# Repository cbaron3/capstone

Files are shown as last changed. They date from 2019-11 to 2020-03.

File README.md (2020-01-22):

# Capstone
Source code for Mechatronic Systems Engineering Capstone project

# Requirements

## Teensyduino

Firmware is written for a Teensy 3.2 and makes use of Teensy features such as PWMServo and elapsedMicros. 

[Teensyduino](https://www.pjrc.com/teensy/teensyduino.html)

## Barometer

Library to interact with the on-board MPL3115A2. 

[MPL3115A2](https://github.com/sparkfun/MPL3115A2_Breakout/tree/master/Libraries/Arduino)

## GPS

Libraries to interact with the on-board Adafruit GPS module. Two were selected: one interrupt-based and one polling-based. The interrupt-based library is what we use.

[Adafruit_GPS - Interrupt based](https://github.com/adafruit/Adafruit_GPS)

[TinyGPS - Polling based](https://github.com/mikalhart/TinyGPS)

## IMU

Library to interact with the on-board MPU9250.

[MPU9250](https://github.com/bolderflight/MPU9250)

## AHRS 

Library to filter our raw IMU data to produce accurate roll/pitch/yaw.

[uNavAHR](https://github.com/bolderflight/uNavAHRS)

[Eigen - Library Dependency](https://github.com/bolderflight/Eigen)

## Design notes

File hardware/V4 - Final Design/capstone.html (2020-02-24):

Partlist exported from C:/Users/cbaro/OneDrive/Documents/Development/aero/capstone/hardware/V4 - Final Design/capstone.sch at 2020-02-19 5:00 PM

Qty | Value | Device | Package | Parts | Description | CREATED_BY | DESCRIPTION | DIGI-KEY_PART_NUMBER | DIGI-KEY_PURCHASE_URL | DIGIKEY_PART_NUMBER | DIGI_KEY_PART_NUMBER | MANUFACTURER | MF | MP | MPN | OC_FARNELL | OC_NEWARK | PACKAGE | POPULARITY | SPICEPREFIX | TP_SIGNAL_NAME
1 | | ANTENNA | PAD-01 | ANT1 | Antenna | | | | | | | | | | | | | | 11
1 | | GPS_FGPMMOPA6H | FGPMMOPA6H | U4 | GPS Module - MTK MT3339 Chipset, -165dBm sensitivity, 22 channels, 10Hz, auto-select external antenna options
1 | | W237-102 | W237-102 | X1 | WAGO SCREW CLAMP | | | | | | | | | | 237-102 | unknown | 70K9898 | | 32
1 | 0.1u | C-USC0603 | C0603 | C3 | CAPACITOR, American symbol
1 | 10 nF | C-USC0603 | C0603 | C9 | CAPACITOR, American symbol
2 | 10 u | C-USC0603 | C0603 | C1, C4 | CAPACITOR, American symbol
1 | 100 n | C-USC0603 | C0603 | C2 | CAPACITOR, American symbol
2 | 100 nF | C-USC0603 | C0603 | C7, C8 | CAPACITOR, American symbol
2 | 100n | C-USC0603 | C0603 | C5, C6 | CAPACITOR, American symbol | | | | | | | | | | | | | | 37 | C
2 | 4.7k | R-US_R0603 | R0603 | R3, R4 | RESISTOR, American symbol
1 | 470 | R-US_R0603 | R0603 | R10 | RESISTOR, American symbol
3 | 61300311121 | 61300311121 | 61300311121 | J1, J2, J3 | CONN HEADER VERT 3POS 2.54MM | PCBLayout.com | | | | | 732-5316-ND | Wurth Electronics Inc. | | | 61300311121
4 | 82 Ohm | R-US_R0603 | R0603 | R1, R2, R11, R12 | RESISTOR, American symbol
1 | BMP388 | BMP388 | PQFN50P200X200X80-10N | U1 | P-Sensor SPI I2C 1, 25 Bar SMD | | P-Sensor SPI I2C 1, 25 Bar SMD | 828-1079-1-ND | https://www.digikey.ca/product-detail/en/bosch-sensortec/BMP388/828-1079-1-ND/8322640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 | | | | Bosch Sensortec | BMP388 | | | | WFLGA-10 Bosch Tools
1 | CH291-1220LF | CH291-1220LF | CH291-1220LF | G1 | Battery Holder, SMT, 12mm | | | | | | | | | | | | | | 1
5 | HSMH-C190 | HSMH-C190 | LED-0603 | LED1, LED2, LED3, LED4, LED5 | LED RED DIFFUSED CHIP SMD | PCBLayout.com | | | | 516-1420-1-ND | | Broadcom Limited | | | HSMH-C190 | | | 0603
1 | LSM9DS1TR | LSM9DS1TR | PQFN43P300X350X102-24N | U2 | The LSM9DS1 is a system-in-package featuring a | | LSM9DS1 Series ±2/±4/±8/±16 g 3D Digital Linear Acceleration Sensor - LGA-24 | 497-14946-1-ND | https://www.digikey.ca/product-detail/en/stmicroelectronics/LSM9DS1TR/497-14946-1-ND/4988079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 | | | | STMicroelectronics | LSM9DS1TR | | | | TFLGA-24 STMicroelectronics
4 | MOUNT-HOLE2.8 | MOUNT-HOLE2.8 | 2,8 | H1, H2, H3, H4 | MOUNTING HOLE with drill center marker
18 | PTR1B1,27 | PTR1B1,27 | B1,27 | TP1, TP2, TP3, TP4, TP5, TP6, TP7, TP8, TP9, TP10, TP11, TP12, TP13, TP14, TP15, TP16, TP17, TP18 | TEST PIN
1 | RFM95W-915S2 | RFM95W-915S2 | XCVR_RFM95W-915S2 | U3 | RFM95(W) - Low Power Long Range Transceiver Module V1.0 | | RFM95W LoRA Transceiver Module 915MHz | RFM95W-915S2-ND | https://www.digikey.ca/product-detail/en/rf-solutions/RFM95W-915S2/RFM95W-915S2-ND/6564923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 | | | | RF Solutions | RFM95W-915S2 | | | | SMD-16 RF Solutions
1 | TEENSY_3.1-3.2_OUTER_ROW | TEENSY_3.1-3.2_OUTER_ROW | TEENSY_3.0-3.2&LC_OUTER_ROW | U$1 | Footprint for Teensy 3.1 or 3.2 board using all pin connections on the outer perimeter

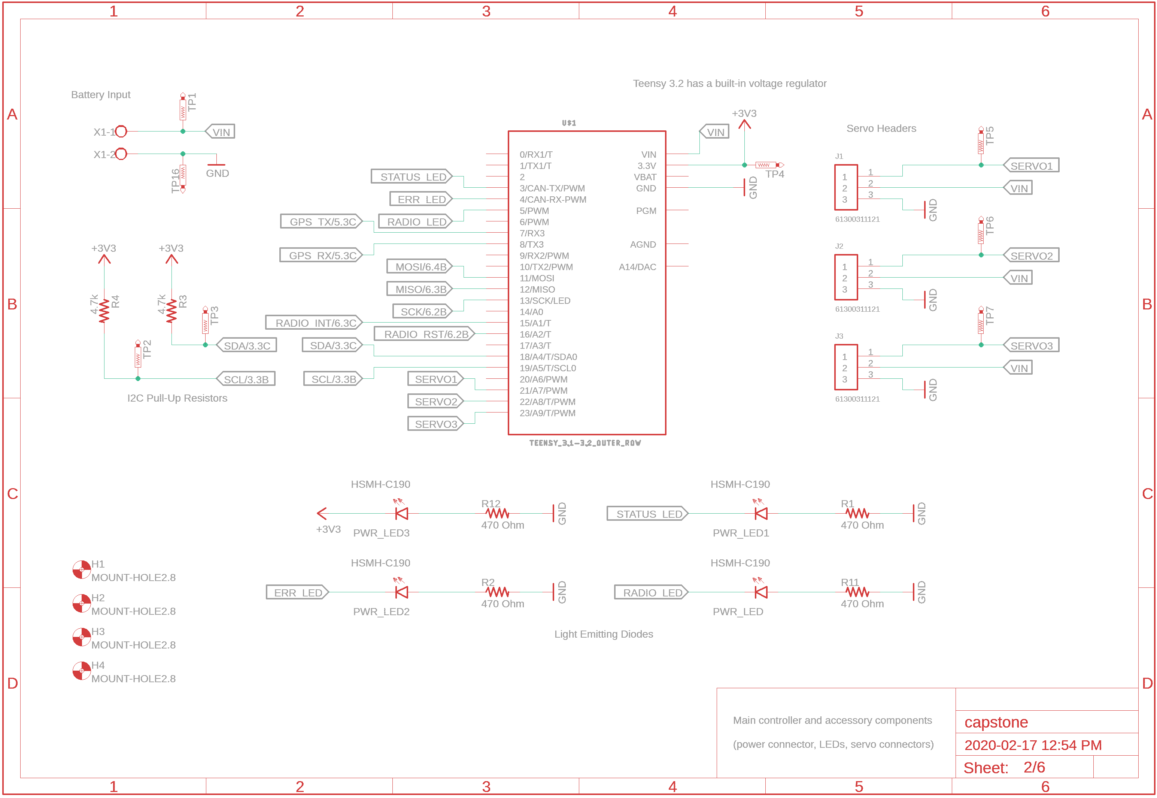
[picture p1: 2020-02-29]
hardware/V4 - Final Design/pics/teensy.png

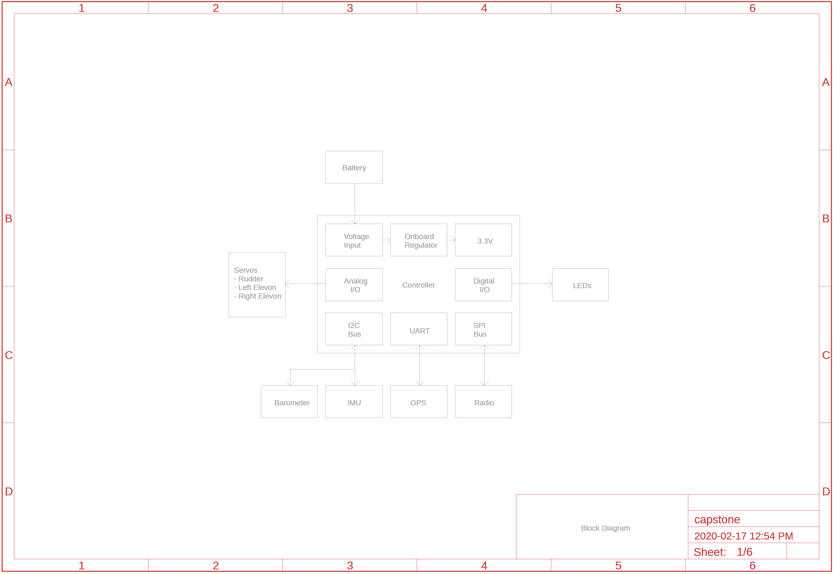
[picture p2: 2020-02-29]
hardware/V4 - Final Design/pics/block-diagram.png

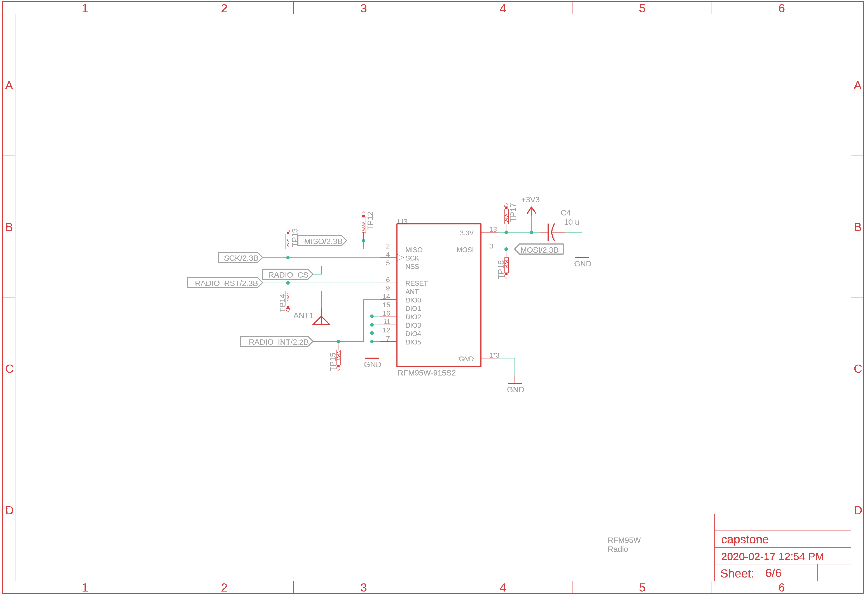
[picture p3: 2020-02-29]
hardware/V4 - Final Design/pics/radio.png

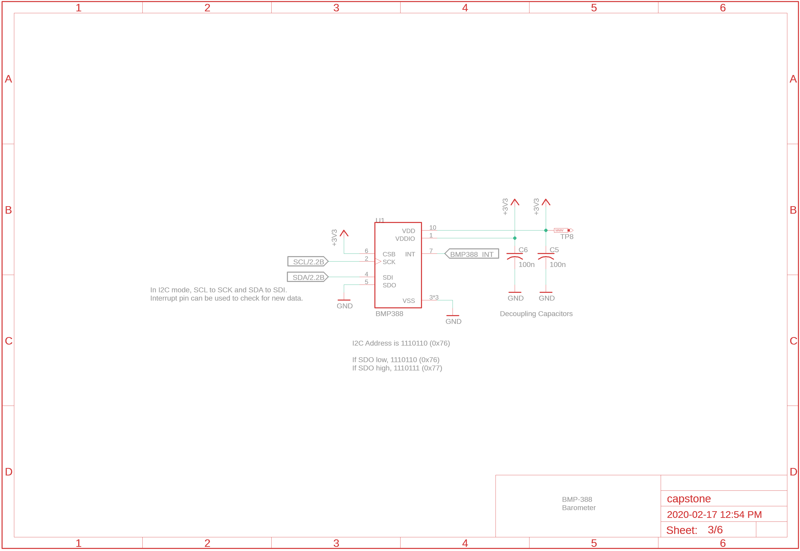
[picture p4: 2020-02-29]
hardware/V4 - Final Design/pics/bmp-388.png

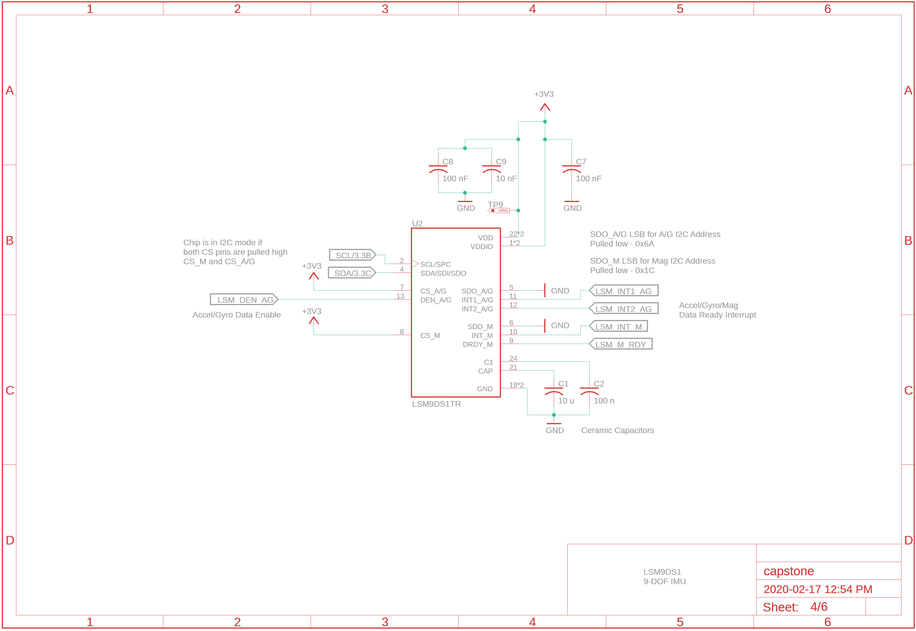
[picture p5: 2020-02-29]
hardware/V4 - Final Design/pics/imu.png

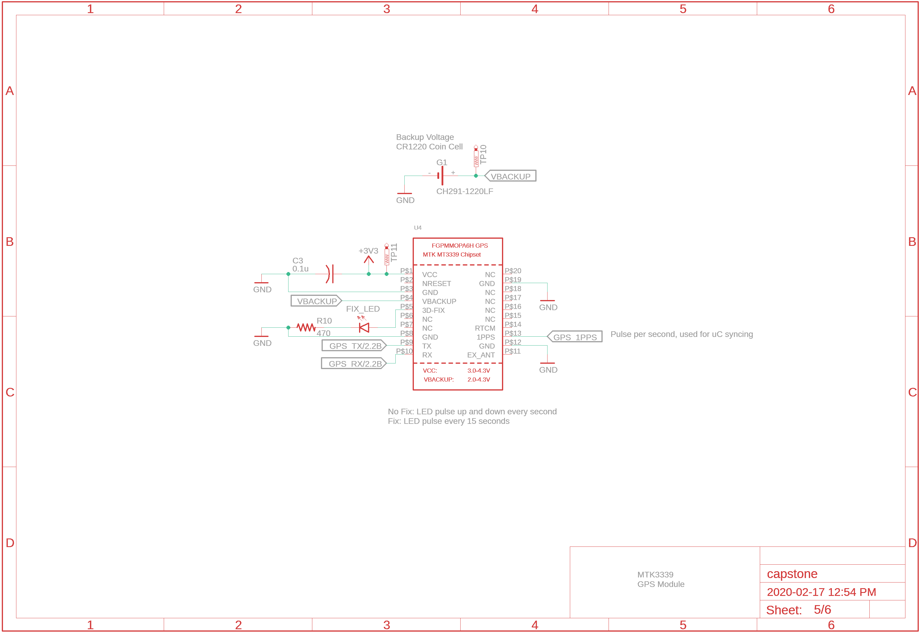
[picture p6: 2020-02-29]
hardware/V4 - Final Design/pics/gps.png

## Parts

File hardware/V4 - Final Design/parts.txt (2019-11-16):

IMU - (LSM9DS1TR) https://www.digikey.ca/product-detail/en/stmicroelectronics/LSM9DS1TR/497-14946-1-ND/4988079
Radio - (RFM95W) https://www.digikey.ca/product-detail/en/rf-solutions/RFM95W-915S2/RFM95W-915S2-ND/6564923
Baro - (BMP388) https://www.digikey.ca/product-detail/en/bosch-sensortec/BMP388/828-1079-1-ND/8322640
GPS - (Adafruit Ultimate GPS) https://www.adafruit.com/product/790
uC - Teensy 3.2

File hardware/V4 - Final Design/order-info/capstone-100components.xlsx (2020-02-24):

Index | Quantity | Part Number | Manufacturer Part Number | Description | Customer Reference | Available | Backorder | Unit Price | Extended Price CAD
1 | 100 | 732-10955-ND | 691137710002 | TERM BLK 2POS SIDE ENTRY 5MM PCB |  | 100 | 0 | 0.3861 | 38.61
2 | 300 | 399-8990-1-ND | C0603C103M4RACTU | CAP CER 10000PF 16V X7R 0603 |  | 300 | 0 | 0.0496 | 14.88
3 | 600 | 399-1098-1-ND | C0603C104Z4VACTU | CAP CER 0.1UF 16V Y5V 0603 |  | 600 | 0 | 0.019 | 11.40
4 | 100 | P470GCT-ND | ERJ-3GEYJ471V | RES SMD 470 OHM 5% 1/10W 0603 |  | 100 | 0 | 0.0292 | 2.92
5 | 200 | P4.70KHCT-ND | ERJ-3EKF4701V | RES SMD 4.7K OHM 1% 1/10W 0603 |  | 200 | 0 | 0.0356 | 7.12
6 | 400 | P82GCT-ND | ERJ-3GEYJ820V | RES SMD 82 OHM 5% 1/10W 0603 |  | 400 | 0 | 0.0238 | 9.52
7 | 500 | 732-4978-1-ND | 150060RS75000 | LED RED CLEAR 0603 SMD |  | 500 | 0 | 0.14156 | 70.78
8 | 100 | BK-885-ND | BK-885 | BATTERY RETAINER COIN 12MM SMD |  | 100 | 0 | 0.419 | 41.90
9 | 100 | 1568-1231-ND | DEV-13736 | TEENSY 3.2 K20 EVAL BRD |  | 100 | 0 | 32.17 | 3217.00
10 | 100 | RFM95W-868S2-ND | RFM95W-868S2 | RF TXRX MODULE ISM<1GHZ |  | 100 | 0 | 22.2 | 2220.00
11 | 100 | 497-14946-1-ND | LSM9DS1TR | IMU ACCEL/GYRO/MAG I2C/SPI 24LGA |  | 100 | 0 | 7.6955 | 769.55
12 | 100 | 828-1079-1-ND | BMP388 | SENSOR PRESSURE ABS |  | 100 | 0 | 3.1608 | 316.08
13 | 300 | 1849-1003-ND | PR20203VBNN | CONN HEADER VERT 3POS 2.54MM |  | 300 | 0 | 0.0473 | 14.19
 |  |  |  |  |  |  |  |  | 6733.95

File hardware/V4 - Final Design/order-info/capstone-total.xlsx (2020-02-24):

Quantity | Board Cost | Component Cost | Total Cost | Cost Per Board
10 | $61.11 | $1112 | $1173.11 | $117.31
25 | $89.23 | $2736.03 | $2825.26 | $113.01
50 | $121.62 | $5428.87 | $5550.49 | $111.01
100 | $182.82 | $10699.95 | $10882.77 | $108.83
500 | $629.33 | $52600.69 | $53230.02 | $106.46

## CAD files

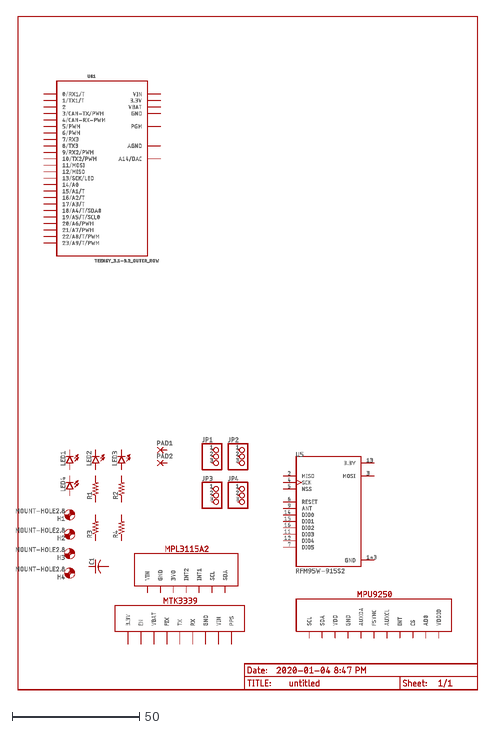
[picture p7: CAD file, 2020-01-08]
hardware/V5 - Prototype Design/untitled.dxf
181.2 x 264.5

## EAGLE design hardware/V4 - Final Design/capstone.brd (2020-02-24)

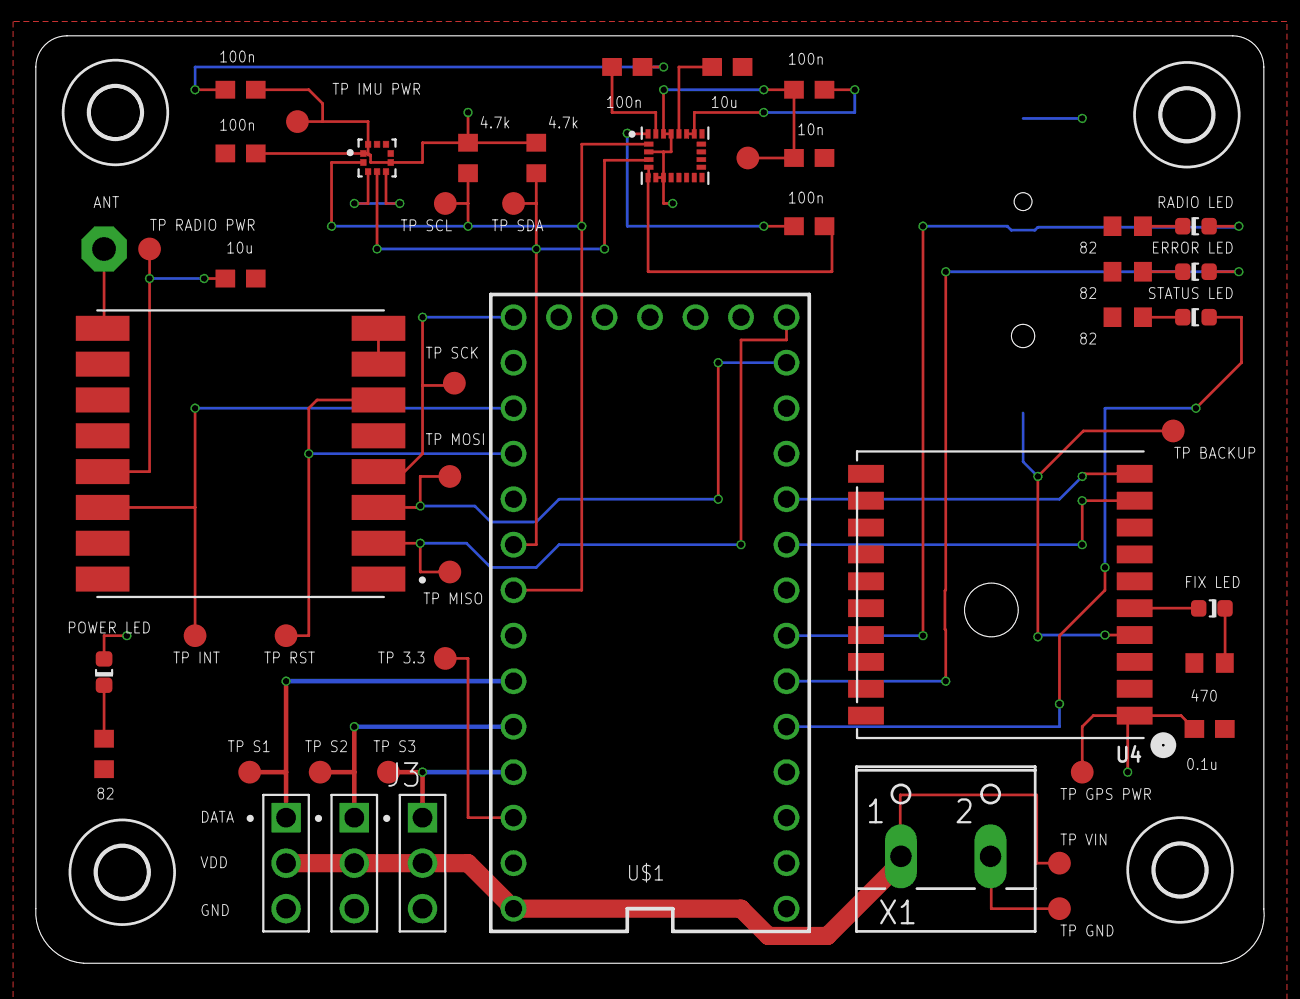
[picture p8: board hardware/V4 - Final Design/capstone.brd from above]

Board: 2 copper layers, 68.6 x 51.8 mm, 54 parts (1 on the bottom side), 28 nets.

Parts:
ANT1: PAD-01
C1, C4: 10 u; C0603
C2: 100 n; C0603
C3: 0.1u; C0603
C5, C6: 100n; C0603
C7, C8: 100 nF; C0603
C9: 10 nF; C0603
G1: CH291-1220LF
H1, H2, H3, H4: MOUNT-HOLE2.8; 2,8
J1, J2, J3: 61300311121
LED1, LED2, LED3, LED4, LED5: HSMH-C190; LED-0603
R1, R2, R11, R12: 82 Ohm; R0603
R3, R4: 4.7k; R0603
R10: 470; R0603
TP1, TP2, TP3, TP4, TP5, TP6, TP7, TP8, TP9, TP10, TP11, TP12, TP13, TP14, TP15, TP16, TP17, TP18: PTR1B1,27; B1,27
U1: BMP388; PQFN50P200X200X80-10N
U2: LSM9DS1TR; PQFN43P300X350X102-24N
U3: RFM95W-915S2; XCVR_RFM95W-915S2
U4: FGPMMOPA6H
U$1: TEENSY_3.1-3.2_OUTER_ROW; TEENSY_3.0-3.2&LC_OUTER_ROW
X1: W237-102

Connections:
+3V3: C3.1, C4.1, C5.1, C6.1, C7.1, C8.1, C9.1, LED1.A, R3.1, R4.1, TP4.TP, TP8.TP, TP9.TP, TP11.TP, TP17.TP, U1.1, U1.6, U1.10, U2.1, U2.3, U2.7, U2.8, U2.22, U2.23, U3.13, U4.P$1, U$1.3.3V, U$1.3.3V1
ERR_LED: LED2.A, U$1.4
GND: C1.2, C2.2, C3.2, C4.2, C5.2, C6.2, C7.2, C8.2, C9.2, G1.-, J1.3, J2.3, J3.3, R1.2, R2.2, R10.1, R11.2, R12.2, TP16.TP, U1.3, U1.5, U1.8, U1.9, U2.5, U2.6, U2.19, U2.20, U3.1, U3.7, U3.8, U3.10, U3.11, U3.12, U3.15, U3.16, U4.P$3, U4.P$8, U4.P$12, U4.P$19, U$1.GND, U$1.GND1, X1.2
GPS_RX: U4.P$10, U$1.8
GPS_TX: U4.P$9, U$1.7
MISO: TP12.TP, U3.2, U$1.12
MOSI: TP18.TP, U3.3, U$1.11
unnamed: C1.1, U2.21
unnamed: C2.1, U2.24
unnamed: LED5.C, R10.2
unnamed: LED5.A, U4.P$5
unnamed: ANT1.1, U3.9
unnamed: LED1.C, R12.1
unnamed: LED2.C, R2.1
unnamed: LED4.C, R11.1
unnamed: LED3.C, R1.1
RADIO_INT: TP15.TP, U3.14, U$1.15/A1
RADIO_LED: LED4.A, U$1.5
RADIO_RST: TP14.TP, U3.6, U$1.16/A2
SCK: TP13.TP, U3.4, U$1.13
SCL: R4.2, TP2.TP, U1.2, U2.2, U$1.19/A5
SDA: R3.2, TP3.TP, U1.4, U2.4, U$1.18/A4
SERVO1: J1.1, TP5.TP, U$1.21/A7
SERVO2: J2.1, TP6.TP, U$1.22/A8
SERVO3: J3.1, TP7.TP, U$1.23/A9
STATUS_LED: LED3.A, U$1.3
VBACKUP: G1.+, TP10.TP, U4.P$4
VIN: J1.2, J2.2, J3.2, TP1.TP, U$1.VIN, X1.1

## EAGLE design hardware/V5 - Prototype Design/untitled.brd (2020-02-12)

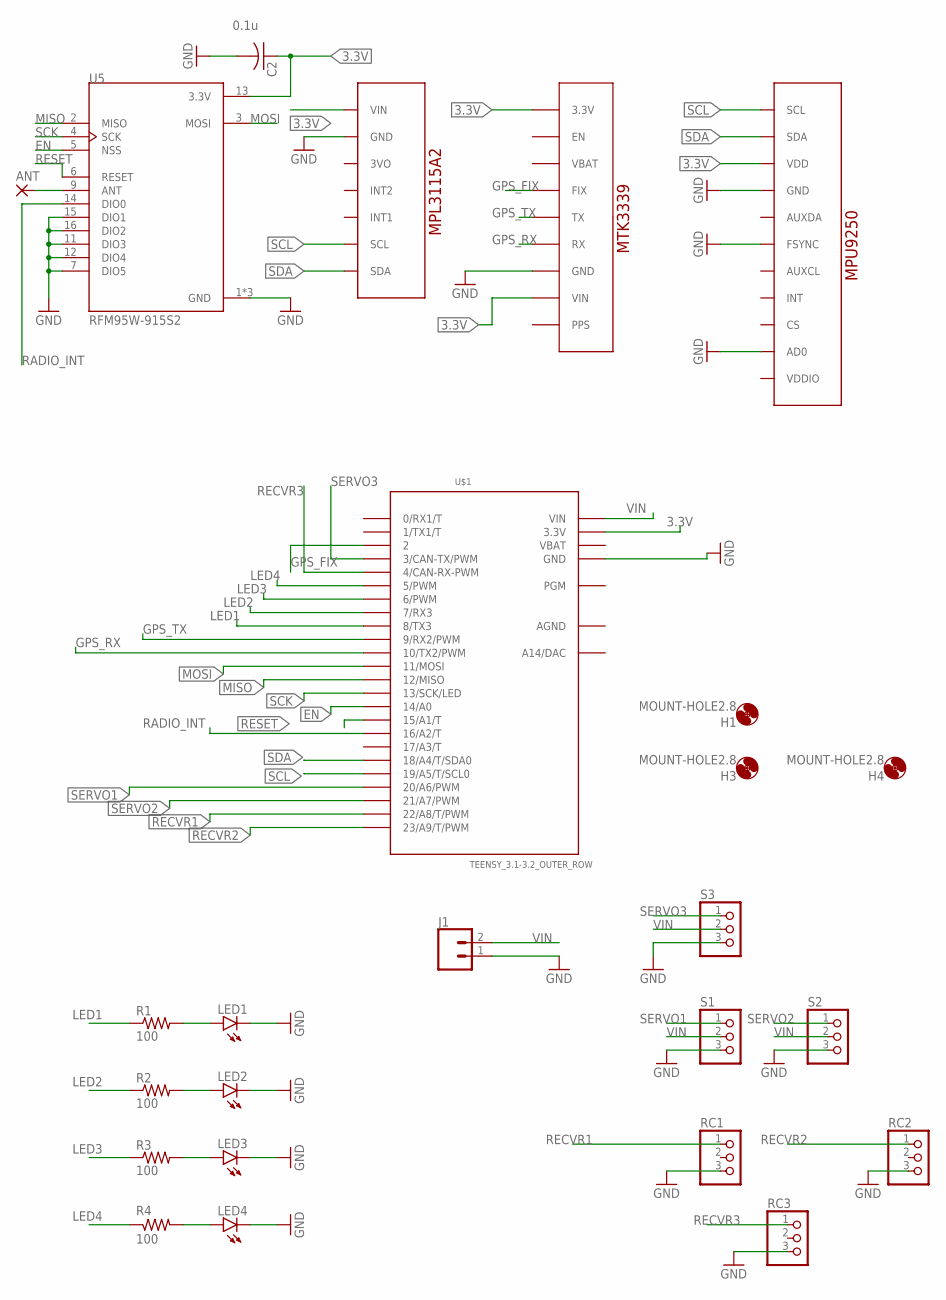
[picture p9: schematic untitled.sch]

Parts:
ANT: 2,54/0,9
C2: 0.1u; C1206
H1, H3, H4: MOUNT-HOLE2.8; 2,8
J1: CONN_025MM; SCREWTERMINAL-5MM-2
LED1, LED2, LED3, LED4: LEDCHIPLED_1206; CHIPLED_1206
R1, R2, R3, R4: 100; M1206
RC1, RC2, RC3: PINHD-1X3; 1X03
S1, S2, S3: PINHD-1X3; 1X03
U1: ADAFRUIT_MPL3115A2_BAROMETER
U2: ADAFRUIT_MTK3339_GPS
U4: SPARKFUN_MPU9250_IMU
U5: RFM95W-915S2; XCVR_RFM95W-915S2
U$1: TEENSY_3.1-3.2_OUTER_ROW; TEENSY_3.0-3.2&LC_OUTER_ROW

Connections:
3.3V: C2.1, U1.VIN, U2.3.3V, U2.VIN, U4.VDD, U5.13 (3.3V), U$1.3.3V, U$1.3.3V1 (3.3V)
AGND: U$1.AGND
EN: U5.5 (NSS), U$1.14/A0
GND: C2.2, J1.1, LED1.C, LED2.C, LED3.C, LED4.C, RC1.3, RC2.3, RC3.3, S1.3, S2.3, S3.3, U1.GND, U2.GND, U4.AD0, U4.FSYNC, U4.GND, U5.1 (GND), U5.7 (DIO5), U5.8 (GND), U5.10 (GND), U5.11 (DIO3), U5.12 (DIO4), U5.15 (DIO1), U5.16 (DIO2), U$1.GND, U$1.GND1 (GND)
GPS_FIX: U2.FIX, U$1.2
GPS_RX: U2.RX, U$1.10 (10/TX2/PWM)
GPS_TX: U2.TX, U$1.9 (9/RX2/PWM)
LED1: R1.1, U$1.8 (8/TX3)
LED2: R2.1, U$1.7 (7/RX3)
LED3: R3.1, U$1.6 (6/PWM)
LED4: R4.1, U$1.5 (5/PWM)
MISO: U5.2 (MISO), U$1.12 (12/MISO)
MOSI: U5.3 (MOSI), U$1.11 (11/MOSI)
unnamed: ANT.1, U5.9 (ANT)
unnamed: LED1.A, R1.2
unnamed: LED2.A, R2.2
unnamed: LED3.A, R3.2
unnamed: LED4.A, R4.2
RADIO_INT: U5.14 (DIO0), U$1.16/A2 (16/A2/T)
RECVR1: RC1.1, U$1.22/A8 (22/A8/T/PWM)
RECVR2: RC2.1, U$1.23/A9 (23/A9/T/PWM)
RECVR3: RC3.1, U$1.4 (4/CAN-RX-PWM)
RESET: U5.6 (RESET), U$1.15/A1 (15/A1/T)
SCK: U5.4 (SCK), U$1.13 (13/SCK/LED)
SCL: U1.SCL, U4.SCL, U$1.19/A5 (19/A5/T/SCL0)
SDA: U1.SDA, U4.SDA, U$1.18/A4 (18/A4/T/SDA0)
SERVO1: S1.1, U$1.20/A6 (20/A6/PWM)
SERVO2: S2.1, U$1.21/A7 (21/A7/PWM)
SERVO3: S3.1, U$1.3 (3/CAN-TX/PWM)
VBAT: U$1.VBAT
VIN: J1.2, S1.2, S2.2, S3.2, U$1.VIN

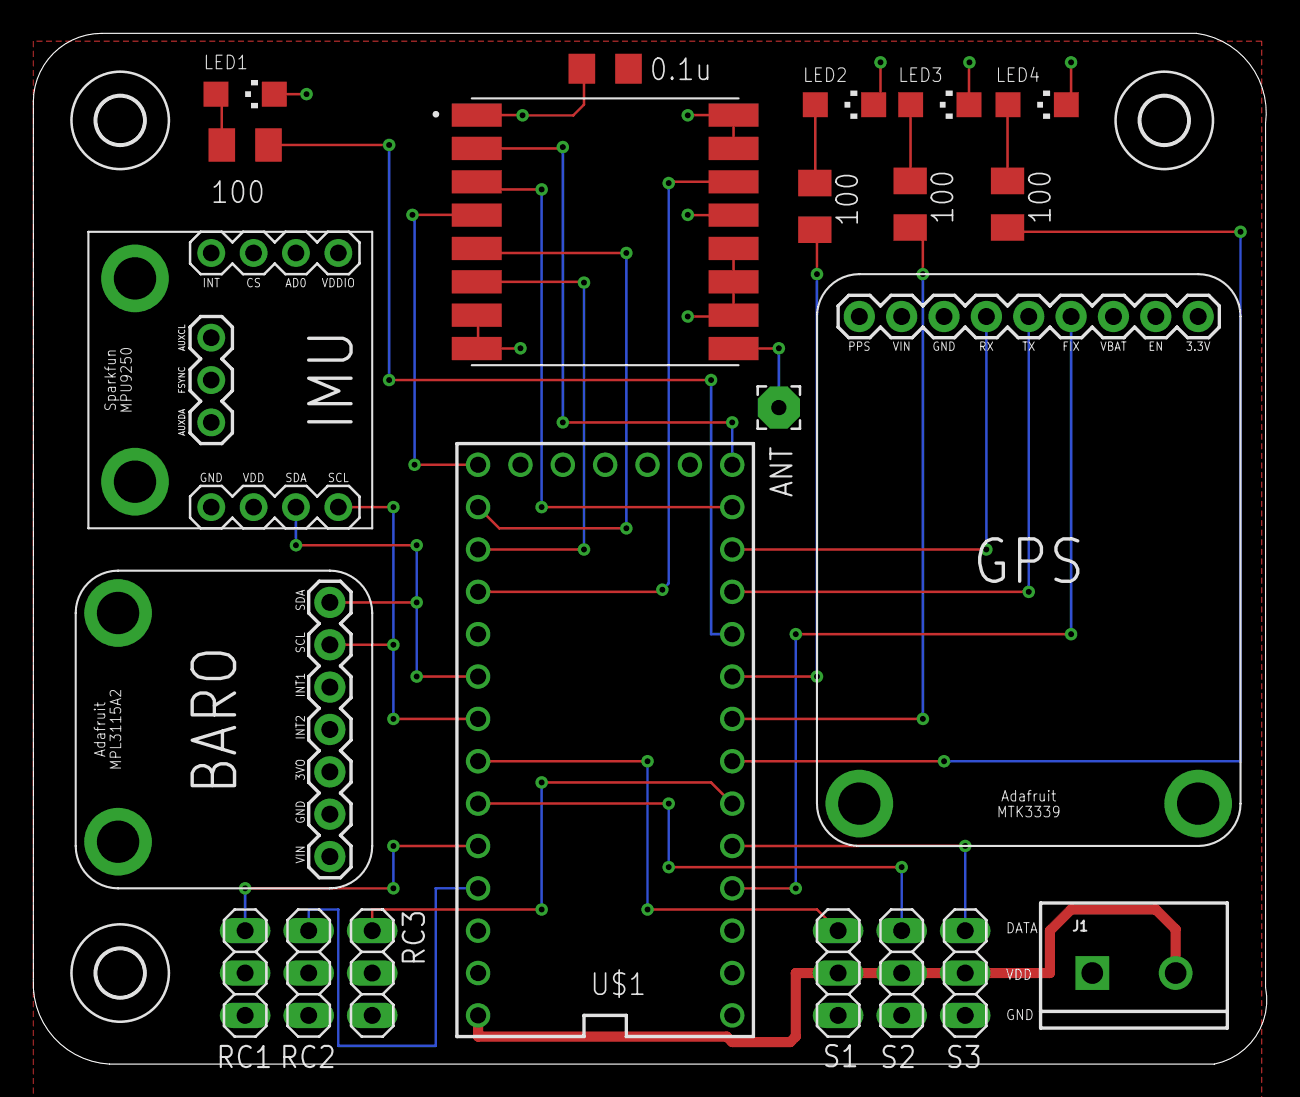
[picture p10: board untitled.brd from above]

Board: 2 copper layers, 74.0 x 61.8 mm, 25 parts (0 on the bottom side), 29 nets.

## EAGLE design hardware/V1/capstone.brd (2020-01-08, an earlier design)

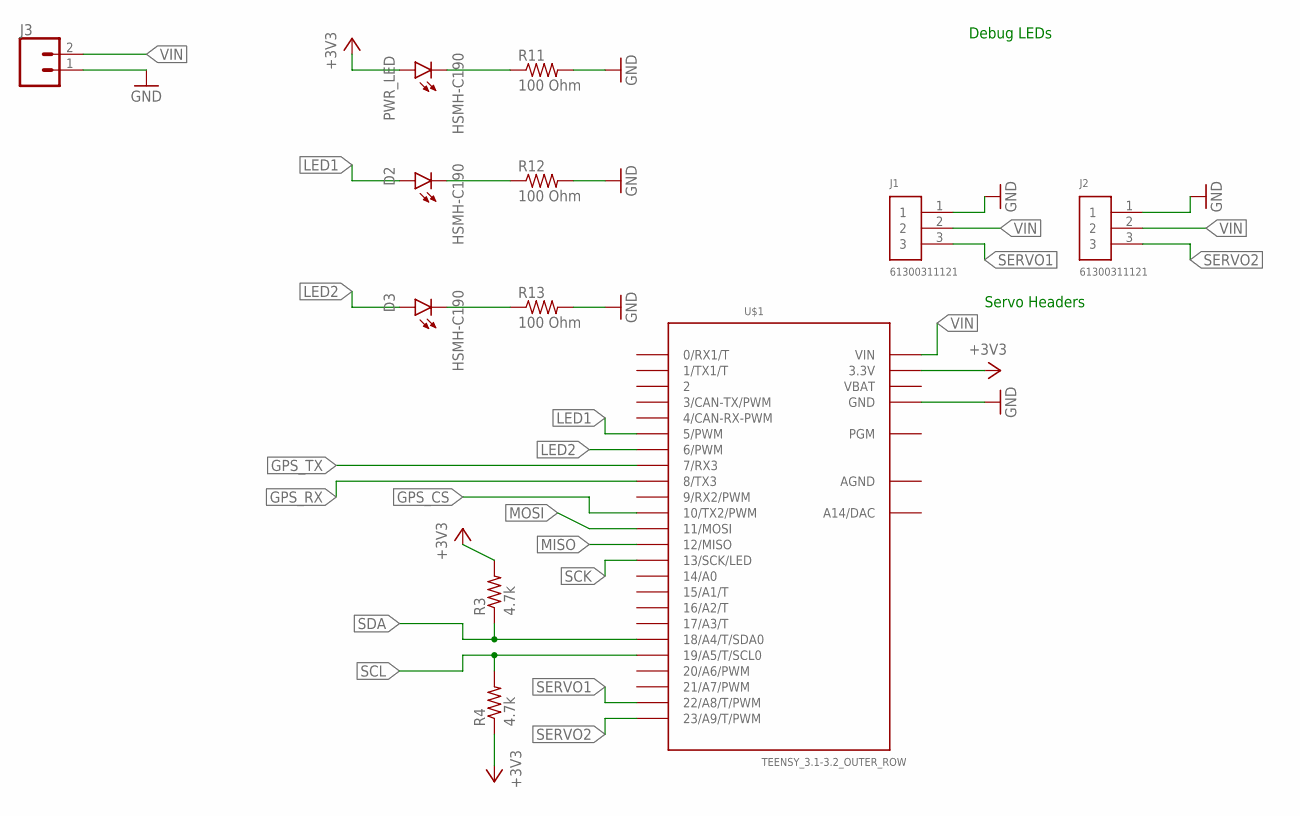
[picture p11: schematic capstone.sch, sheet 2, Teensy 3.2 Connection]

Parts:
D2, D3: HSMH-C190; LED-0603
J1, J2: 61300311121
J3: CONN_02; 1X02
PWR_LED: HSMH-C190; LED-0603
R3, R4: 4.7k; R0603
R11, R12, R13: 100 Ohm; R0603
U$1: TEENSY_3.1-3.2_OUTER_ROW; TEENSY_3.0-3.2&LC_OUTER_ROW

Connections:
+3V3: PWR_LED.A, R3.2, R4.1, U$1.3.3V, U$1.3.3V1 (3.3V); also elsewhere on the board
AGND: U$1.AGND
GND: J1.1, J2.1, J3.1, R11.2, R12.2, R13.2, U$1.GND, U$1.GND1 (GND); also elsewhere on the board
GPS_CS: U$1.10 (10/TX2/PWM); also elsewhere on the board
GPS_RX: U$1.8 (8/TX3); also elsewhere on the board
GPS_TX: U$1.7 (7/RX3); also elsewhere on the board
LED1: D2.A, U$1.5 (5/PWM)
LED2: D3.A, U$1.6 (6/PWM)
MISO: U$1.12 (12/MISO); also elsewhere on the board
MOSI: U$1.11 (11/MOSI); also elsewhere on the board
unnamed: PWR_LED.C, R11.1
unnamed: D2.C, R12.1
unnamed: D3.C, R13.1
SCK: U$1.13 (13/SCK/LED); also elsewhere on the board
SCL: R4.2, U$1.19/A5 (19/A5/T/SCL0); also elsewhere on the board
SDA: R3.1, U$1.18/A4 (18/A4/T/SDA0); also elsewhere on the board
SERVO1: J1.3, U$1.22/A8 (22/A8/T/PWM)
SERVO2: J2.3, U$1.23/A9 (23/A9/T/PWM)
VBAT: U$1.VBAT
VIN: J1.2, J2.2, J3.2, U$1.VIN

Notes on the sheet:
Servo Headers
Debug LEDs

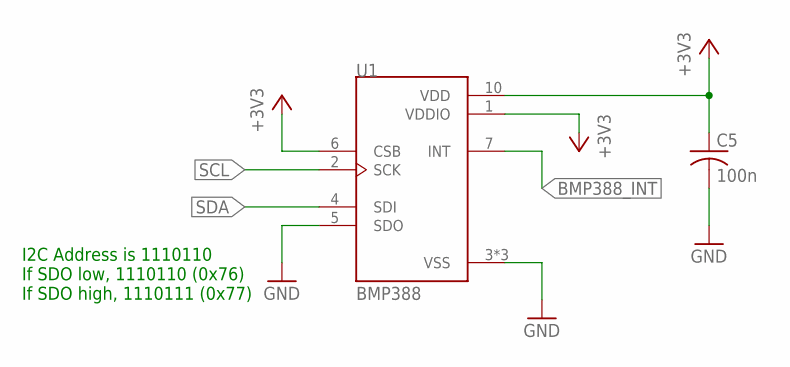
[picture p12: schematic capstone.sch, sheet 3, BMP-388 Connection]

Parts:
C5: 100n; C0603
U1: BMP388; PQFN50P200X200X80-10N

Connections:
+3V3: C5.1, U1.1 (VDDIO), U1.6 (CSB), U1.10 (VDD); also elsewhere on the board
BMP388_INT: U1.7 (INT)
GND: C5.2, U1.3 (VSS), U1.5 (SDO), U1.8 (VSS), U1.9 (VSS); also elsewhere on the board
SCL: U1.2 (SCK); also elsewhere on the board
SDA: U1.4 (SDI); also elsewhere on the board

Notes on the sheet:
I2C Address is 1110110 If SDO low, 1110110 (0x76) If SDO high, 1110111 (0x77)

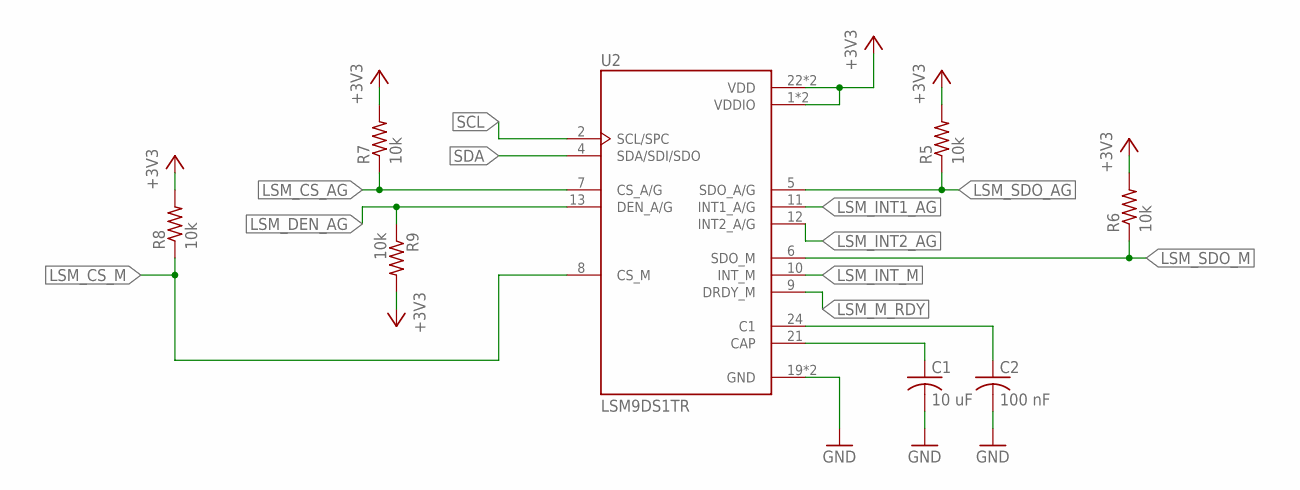
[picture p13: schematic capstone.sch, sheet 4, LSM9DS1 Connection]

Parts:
C1: 10 uF; C0603
C2: 100 nF; C0603
R5, R6, R7, R8, R9: 10k; R0603
U2: LSM9DS1TR; PQFN43P300X350X102-24N

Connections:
+3V3: R5.2, R6.2, R7.2, R8.2, R9.2, U2.1 (VDDIO), U2.3 (VDDIO), U2.22 (VDD), U2.23 (VDD); also elsewhere on the board
GND: C1.2, C2.2, U2.19 (GND), U2.20 (GND); also elsewhere on the board
LSM_CS_AG: R7.1, U2.7 (CS_A/G)
LSM_CS_M: R8.1, U2.8 (CS_M)
LSM_DEN_AG: R9.1, U2.13 (DEN_A/G)
LSM_INT1_AG: U2.11 (INT1_A/G)
LSM_INT2_AG: U2.12 (INT2_A/G)
LSM_INT_M: U2.10 (INT_M)
LSM_M_RDY: U2.9 (DRDY_M)
LSM_SDO_AG: R5.1, U2.5 (SDO_A/G)
LSM_SDO_M: R6.1, U2.6 (SDO_M)
unnamed: C1.1, U2.21 (CAP)
unnamed: C2.1, U2.24 (C1)
SCL: U2.2 (SCL/SPC); also elsewhere on the board
SDA: U2.4 (SDA/SDI/SDO); also elsewhere on the board

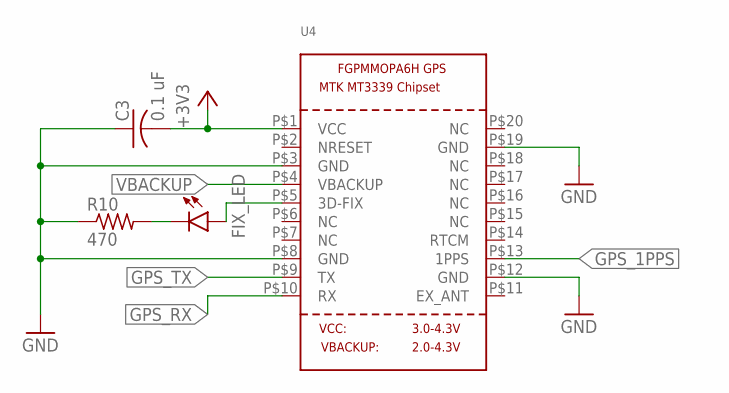
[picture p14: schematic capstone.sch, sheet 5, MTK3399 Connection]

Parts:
C3: 0.1 uF; C0603
FIX_LED: HSMH-C190; LED-0603
R10: 470; R0603
U4: GPS_FGPMMOPA6H; FGPMMOPA6H

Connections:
+3V3: C3.2, U4.P$1 (VCC); also elsewhere on the board
GND: C3.1, R10.1, U4.P$3 (GND), U4.P$8 (GND), U4.P$12 (GND), U4.P$19 (GND); also elsewhere on the board
GPS_1PPS: U4.P$13 (1PPS)
GPS_RX: U4.P$10 (RX); also elsewhere on the board
GPS_TX: U4.P$9 (TX); also elsewhere on the board
unnamed: FIX_LED.C, R10.2
unnamed: FIX_LED.A, U4.P$5 (3D-FIX)
VBACKUP: U4.P$4 (VBACKUP)

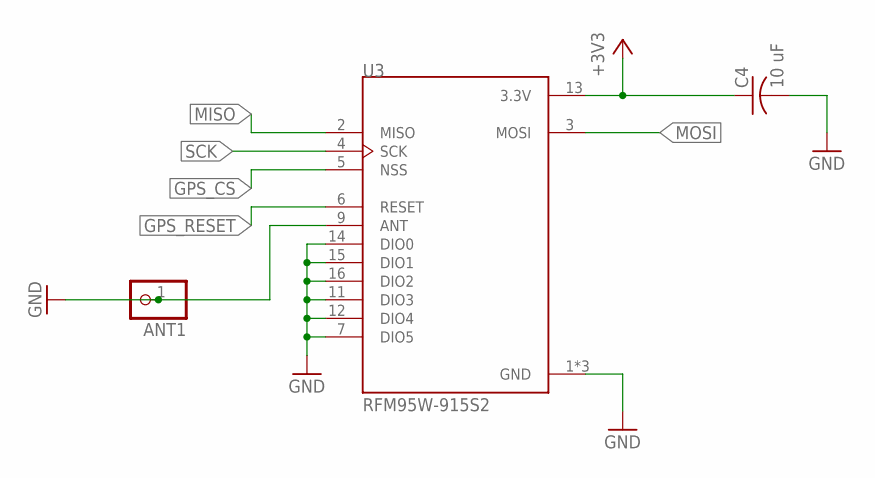
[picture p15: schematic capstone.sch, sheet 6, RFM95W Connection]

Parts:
ANT1: PINHD-1X1; 1X01
C4: 10 uF; C0603
U3: RFM95W-915S2; XCVR_RFM95W-915S2

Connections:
+3V3: C4.1, U3.13 (3.3V); also elsewhere on the board
GND: ANT1.1, C4.2, U3.1 (GND), U3.7 (DIO5), U3.8 (GND), U3.9 (ANT), U3.10 (GND), U3.11 (DIO3), U3.12 (DIO4), U3.14 (DIO0), U3.15 (DIO1), U3.16 (DIO2); also elsewhere on the board
GPS_CS: U3.5 (NSS); also elsewhere on the board
GPS_RESET: U3.6 (RESET)
MISO: U3.2 (MISO); also elsewhere on the board
MOSI: U3.3 (MOSI); also elsewhere on the board
SCK: U3.4 (SCK); also elsewhere on the board

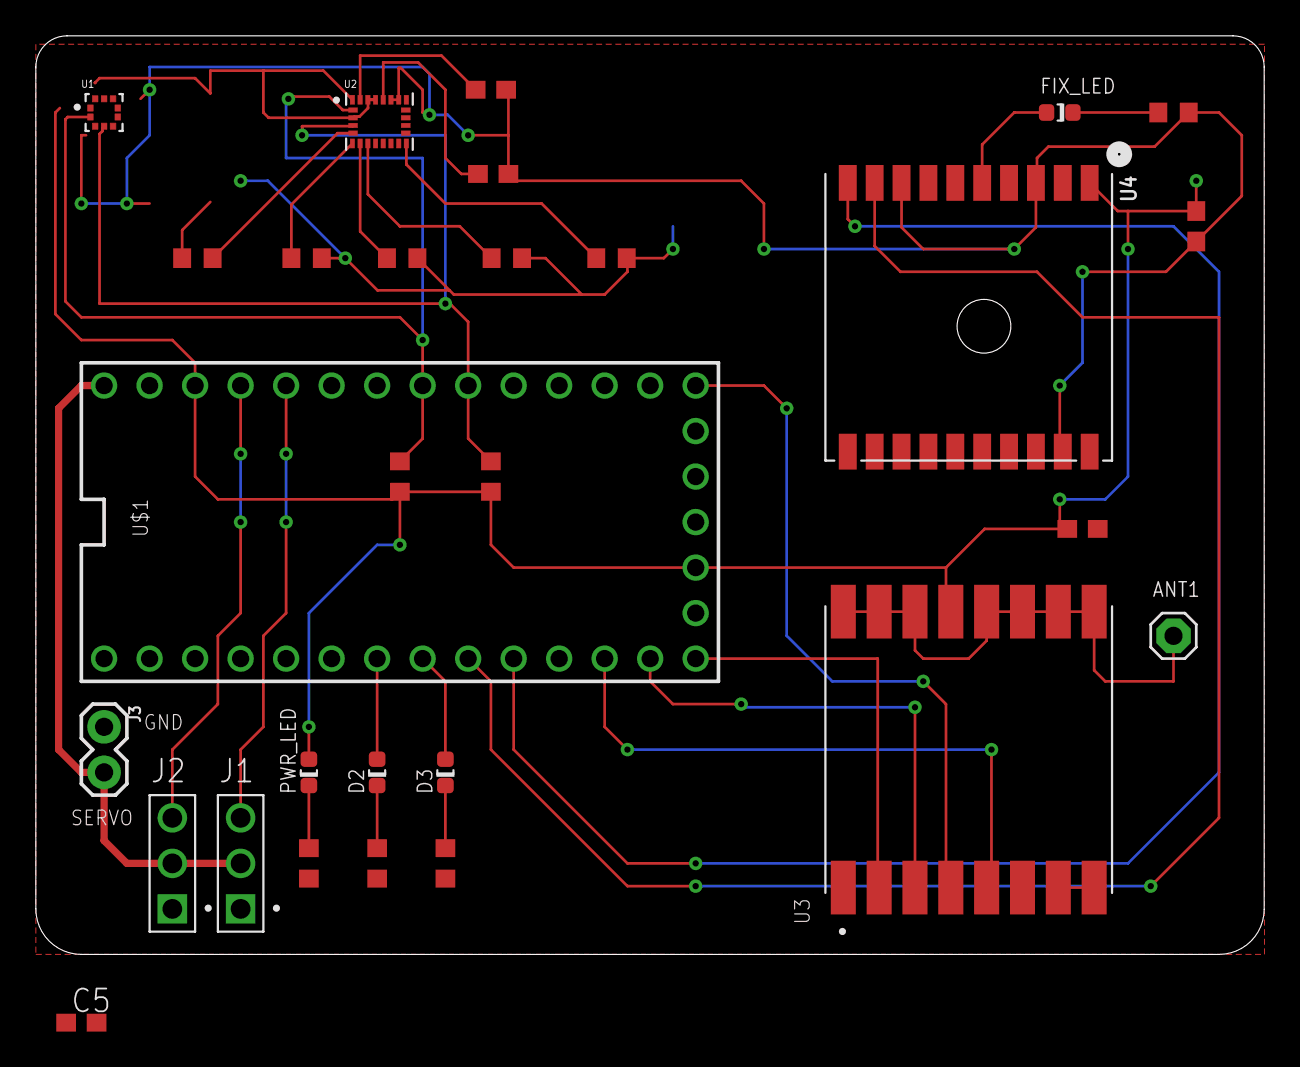
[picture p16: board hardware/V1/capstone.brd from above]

Board: 2 copper layers, 68.6 x 51.3 mm, 29 parts (0 on the bottom side), 27 nets.

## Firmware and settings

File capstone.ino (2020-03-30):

#include "src/aero-cpp-lib/include/Utility.hpp"

// System configuration including pins, debugging, and system mode
#include "Config.hpp"

// Testing out the performance of adding an exponential averaging filter
#include "src/EWMA/Ewma.h"
//Ewma roll_filter(1.0), pitch_filter(1.0), yaw_filter(1.0), left_filter(0.9), right_filter(0.9);

// IMU functionality based on the MPU9250
#include "IMU.hpp"
MPU9250 mpu9250{Wire, 0x68};
uNavAHRS filter;  // Kalman filter for IMU data

// GPS functionalty based on Adafruit GPS using AdafruitGPS interrupt library
#include "GPS.hpp"
Adafruit_GPS adafruit_gps(GPS_PORT);

// Other GPS implementation using TinyGPS instead. Not ideal cause requires you to spend time waiting for buffer to fill
#include "OtherGPS.hpp"

// Barometer functionality based on the MPL3115AS
#include "Barometer.hpp"
MPL3115A2 mpl3115;

// Pins reading PWM from the RC receiver
#include "Receiver.hpp"

// Servo functionality
#include "Actuators.hpp"
Servo left_elevon, right_elevon, rudder;

// Radio usage
#include "Radio.hpp"
aero::def::Status_t status;
RH_RF95 radio {RADIO_CS, RADIO_INT};

// LED usage
#include "LEDS.hpp"

// PID controller usage
#include "Controller.hpp"

// Setpoint calculator
#include "Setpoint.hpp"

// Controller input
volatile float new_yaw = 0.0f, new_pitch = 0.0f, new_roll = 0.0f;

// Controller for pitch
PID roll_control(&CONTROLLER::roll_input, 
                 &CONTROLLER::roll_output, 
                 &CONTROLLER::roll_setpoint, 
                 ROLL_KP, ROLL_KI, ROLL_KD, DIRECT);

// Controller for roll
PID pitch_control(&CONTROLLER::pitch_input, 
                 &CONTROLLER::pitch_output, 
                 &CONTROLLER::pitch_setpoint, 
                 PITCH_KP, PITCH_KI, PITCH_KD, DIRECT);

// Controller for yaw
PID yaw_control(&CONTROLLER::yaw_input, 
                 &CONTROLLER::yaw_output, 
                 &CONTROLLER::yaw_setpoint, 
                 YAW_KP, YAW_KI, YAW_KD, DIRECT);

// Threads
#include "Threads.hpp"

// System mode; auto or manual
mode_type mode = DEFAULT_MODE;

/********************************************/
/* Thread for handling radio communications */ 
/********************************************/

volatile aero::def::ParsedMessage_t* msg; // Poitner to last received message
volatile bool new_msg = false;            // Flag to notify that a new message has been arrived

// Message handler for building a response
volatile aero::Message message_handler;


void thread_radio() {
  // Wait so thread does not start right away
  delay(THREAD_DELAY_MS);
  DEBUG_PRINTLN("Radio thread started");

  
  unsigned long prev = 0, curr = 0;
  aero::def::RawMessage_t server_response;
  
  // Thread loop
  while(true) {
    
    // Check radio on interval
    curr = millis();
    if(curr - prev >= RADIO_INTERVAL_MS) { 
      prev = curr;

      // Keep checking for a new radio message
      msg = RADIO::receive(radio);
      DEBUG_PRINTLN("Checked radio...");
      if( msg != NULL ) {

        // Only accept message if it was addressed to this grlider
        if(msg->m_to == THIS_DEVICE) {
          DEBUG_PRINTLN("New Radio Message");

          // Build response and set flag if response was succesfully sent
          server_response = message_handler.build(THIS_DEVICE, aero::def::ID::Gnd);

          LEDS::on(RADIO_LED);

          bool sent = RADIO::respond(radio, server_response);

          LEDS::off(RADIO_LED);

          new_msg = sent;
        } 
      }
    }

    // Yield current thread if not executing
    threads.yield(); 
    
  }
}

/******************************/
/* Thread for polling the GPS */ 
/******************************/

GPS::Data gps_data; 
volatile bool new_gps = false;

void thread_gps() {
  // Wait so thread does not start right away
  delay(THREAD_DELAY_MS+250);
  DEBUG_PRINTLN("GPS thread started");

  unsigned long prev = 0, curr = 0;
  
  // Thread loop
  while(true) {

    // Check if new gps data is available to parse
    if(GPS::check(adafruit_gps) == true && new_gps == false) {
      
      // Limit update rate for GPS to make sure parsing is not affected
      curr = millis();
      if(curr - prev >= GPS_INTERVAL_MS) {
        prev = curr;
  
        // Read data
        gps_data = GPS::read(adafruit_gps);

        new_gps = true;

      } 
    }

    // Yield current thread if not executing
    threads.yield(); 
    
  }
}

/*************************************/
/* Thread for polling the I2C sensor */ 
/*************************************/
IMU::Data imu_data;
BARO::Data baro_data;

// Flags to indicate when there is new barometer and imu data
volatile bool new_imu = false;
volatile bool new_baro = false;

void thread_i2c() {
  // Wait so thread does not start right away
  delay(THREAD_DELAY_MS+500);
  DEBUG_PRINTLN("I2C thread started");

  unsigned long prev_imu = 0, curr_imu = 0;
  unsigned long prev_baro = 0, curr_baro = 0;

  // Thread loop
  while(true) {
    
    // Only update IMU when data has been processed by filter; hence the flag
    if(new_imu == false) {

      // Keep fixed update rate
      curr_imu = millis();
      if(curr_imu - prev_imu >= IMU_SAMPLE_INTERVAL_MS) {
        prev_imu = curr_imu;

        // Read data
        imu_data = IMU::read(mpu9250);
        
        new_imu = true;
      }
    } 
    
    // Keep fixed update rate
    curr_baro = millis();
    if(curr_baro - prev_baro >= BARO_SAMPLE_INTERVAL_MS) {
      prev_baro = curr_baro;

      baro_data = BARO::read(mpl3115);
    }

    // Yield current thread if not executing
    threads.yield();

  }
}

/********************************************/
/* Thread for handling manual servo control */ 
/********************************************/

void thread_manual() {
  // Wait so thread does not start right away
  delay(THREAD_DELAY_MS+750);
  DEBUG_PRINTLN("Manual thread started");

  unsigned long prev = 0, curr = 0;
  RECEIVER::Data recv_data;
  
  // Thread loop
  while(true) {

    curr = millis();
    if(curr - prev >= MANUAL_INTERVAL_MS) {
      prev = curr;

      // Read data from the receiver
      recv_data = RECEIVER::read();

      ACTUATORS::command_deg(left_elevon, 90);
      ACTUATORS::command_deg(right_elevon, 90);
      ACTUATORS::command_deg(rudder, 90);
    } 
  }
}

/************************************************************************************/
/* Thread for automatic control; stabilization (CURRENTLY ONLY TESTING PITCH, ROLL) */ 
/************************************************************************************/

// Flag to track if the filter has produced updated yaw, pitch, and roll values
volatile bool updated = false;

// Initial position of the elevon motors
float last_left_output = 0.0f, last_right_output = 0.0f;
float left_output = 90.0f, right_output = 90.0f, rudder_output = 0.0f;

void thread_auto() {
  // Wait so thread does not start right away
  delay(THREAD_DELAY_MS+750);
  DEBUG_PRINTLN("Auto thread started");

  unsigned long curr = 0, prev = 0;

  while(true) {

    curr = millis();
    if(curr - prev >= AUTO_INTERVAL_MS && updated == false) {
      prev = curr;
  
      float left_target = 0.0f, right_target = 0.0f, rudder_target = 0.0f;

      // Apply mixing if needed
      #if defined(TEST_TRAINER)
        left_target = (-1*CONTROLLER::pitch_output) + 90.0f;
        // left_target = left_filter.filter(left_target);
        right_target = (-1*CONTROLLER::roll_output) + 90.0f;
        // right_target = right_filter.filter(right_target);
        rudder_target = (-1*CONTROLLER::yaw_output);
      #else
        // Elevon mixing
        left_target = ((CONTROLLER::roll_output + CONTROLLER::pitch_output) / 2.0f) + 90.0f;
        right_target = ((CONTROLLER::roll_output - CONTROLLER::pitch_output) / 2.0f) + 90.0f;
        rudder_target = (-1*CONTROLLER::yaw_output);
      #endif

      // Map output angle to servo millisecond value
      unsigned long left_signal = (unsigned long) map_generic(left_target, SERVO_MIN_ANGLE, SERVO_MAX_ANGLE, SERVO_MIN_MS, SERVO_MAX_MS) - LEFT_ELEVON_MS_OFFSET;
      unsigned long right_signal = (unsigned long) map_generic(right_target, SERVO_MIN_ANGLE, SERVO_MAX_ANGLE, SERVO_MIN_MS, SERVO_MAX_MS) - RIGHT_ELEVON_MS_OFFSET;
      // unsigned long rudder_signal = (unsigned long) map_generic(rudder_output, SERVO_MIN_ANGLE, SERVO_MAX_ANGLE, SERVO_MIN_MS, SERVO_MAX_MS);

      if((int)last_left_output != (int)left_target) {
        ACTUATORS::command_ms(left_elevon, left_signal);
        last_left_output = left_target;
      }

      if((int)last_right_output != (int)right_target) {
        ACTUATORS::command_ms(right_elevon, right_signal);
        last_right_output = right_target;
      }
      
      // ACTUATORS::command_ms(right_elevon, right_signal);
      // ACTUATORS::command_ms(rudder, left_signal);

      updated = true;
    } threads.yield();
  }  
}

/*************************************/
/* Thread for calculating setpoints */ 
/************************************/

void thread_setpoint() {
  // Wait so thread does not start right away
  delay(THREAD_DELAY_MS+1000);
  DEBUG_PRINTLN("Setpoint thread started");

  bool updated = false;

  SETPOINT::Angles plane_angle, to_target_angle;

  // Thread loop
//  while(true) {
//    if(new_gps == true) {
//      /* Compute setpoint here */
//      
//      if(gps_data.fix == true) {
//         updated = SETPOINT::update(gps_data.coord.lat, gps_data.coord.lon, baro_data.delta_altitude);
//
//         if(updated = true){
//            // Get target and plane angles
//            plane_angle = SETPOINT::get_plane_angle();
//            to_target_angle = SETPOINT::get_target_angle();
//
//            // CONTROLLER::roll_setpoint = ...;
//            // CONTROLLER::pitch_setpoint = ...;
//            // CONTROLLER::yaw_setpoint = ...;
//         }
//      }
//      
//      new_gps = false;
//    }
//
//    // Yield current thread if not executing
//    threads.yield();
//  }
}

/**************************************/
/* Thread for signallng CPU activity */ 
/*************************************/
void thread_activity() {
  DEBUG_PRINTLN("Activity thread started");

  while(true) {
    LEDS::on(ACTIVITY_LED);
    threads.delay(500); // Calls yield for 500 ms
    LEDS::off(ACTIVITY_LED);
    threads.delay(500);
  }
}

void thread_debug() {
  // Wait so thread does not start right away
  delay(THREAD_DELAY_MS-250);
  DEBUG_PRINTLN("Debug thread started");

  unsigned long curr = 0, prev = 0;
  while(true) {
    curr = millis();
    if(curr - prev >= DEBUG_INTERVAL_MS) {
      prev = curr;
      IMU::print(imu_data);
      BARO::print(baro_data);
      GPS::print(gps_data);
      
    }

    // Yield current thread if not executing
    threads.yield();
  }
}

void elevons_up() {
  DEBUG_PRINTLN("Elevons up");
  left_elevon.write(SAFETY_LEFT_ELEVON_ANGLE);
  right_elevon.write(SAFETY_RIGHT_ELEVON_ANGLE);
  rudder.write(SAFETY_RUDDER_ANGLE);
}

void elevons_level() {
  DEBUG_PRINTLN("Elevons level");
  left_elevon.write(DEFAULT_LEFT_ELEVON_ANGLE);
  right_elevon.write(DEFAULT_RIGHT_ELEVON_ANGLE);
  rudder.write(DEFAULT_RUDDER_ANGLE);
}

void to_safety_mode(void) {
  // Cancel all motor threads
  THREADS::suspend(AUTO_ID);
  THREADS::suspend(SETPOINT_ID);
  
  THREADS::suspend(MANUAL_ID);
  RECEIVER::terminate_interrupts();

  elevons_up();

  // Update mode
  mode = MODE_SAFETY;
  LEDS::off(MODE_LED);
}

void to_auto_mode(void) {
  THREADS::restart(AUTO_ID);
  THREADS::restart(SETPOINT_ID);

  THREADS::suspend(MANUAL_ID);
  RECEIVER::terminate_interrupts();

  mode = MODE_AUTO;
  LEDS::off(MODE_LED);
}

void to_manual_mode(void) {
  THREADS::suspend(AUTO_ID);
  THREADS::suspend(SETPOINT_ID);

  RECEIVER::start_interrupts();
  THREADS::restart(MANUAL_ID);

  mode = MODE_MANUAL;
  LEDS::on(MODE_LED);
}

void to_idle_mode(void) {
  THREADS::suspend(AUTO_ID);
  THREADS::suspend(SETPOINT_ID);

  THREADS::suspend(MANUAL_ID);
  RECEIVER::terminate_interrupts();

  elevons_level();

  mode = MODE_IDLE;
  LEDS::off(MODE_LED);
}

void glider_state_machine(uint8_t command) {
  using namespace aero;
  using namespace aero::def;

  DEBUG_PRINT("Command: "); DEBUG_PRINTLN(command);

  switch(mode) {
    // In IDLE mode, sensors are being polled. Can move into AUTO state when Pitch:5 (ENGAGE/DISENGAGE)
    case MODE_IDLE: {
      if(command == CMD_TOGGLE_ENGAGE) {
        bit::set(status.state, STATE_ENGAGED_MODE);
        message_handler.add_status(status);
        to_auto_mode();
      } else if( (1== aero::bit::read(command, CMD_PITCH_UP_GLIDER1) && THIS_DEVICE == ID::G1) || 
                 (1 == aero::bit::read(command, CMD_PITCH_UP_GLIDER2) && THIS_DEVICE == ID::G2) ) {
        to_safety_mode();
      }
    } break;

    // In AUTO mode, sensors are being polled and elevons react to orientation.
    // Can move into
      // IDLE when Pitch:5 (ENGAGE/DISENGAGE). Stop auto thread, elevons level
      // MANUAL when Pitch:7 (MODE SWAP). Stop auto thread, start interrupts, start manual thread
      // SAFETY when Pitch:0/1 dependeing on device. Stop auto thread, elevons up
    case MODE_AUTO: {
      if(command == CMD_TOGGLE_ENGAGE) {
        to_idle_mode();
      } else if(1 == aero::bit::read(command, CMD_MODE_SWAP)) {
        to_manual_mode();
      } else if( (1== aero::bit::read(command, CMD_PITCH_UP_GLIDER1) && THIS_DEVICE == ID::G1) || 
                 (1 == aero::bit::read(command, CMD_PITCH_UP_GLIDER2) && THIS_DEVICE == ID::G2) ) {
        to_safety_mode();
      }

    } break;

    // In MANUAL mode, sensors are being polled but elevons react to receiver inputs.
    // Can move into
      // AUTO when Pitch:7 (MODE SWAP). Stop manual thread, stop interrupts, start auto thread
      // SAFETY when Pitch:0/1 depending on device. Stop manual thread, stop interrupts, elevons up
    case MODE_MANUAL: {
      if(1 == aero::bit::read(command, CMD_MODE_SWAP)) {
        to_auto_mode();
      } else if( (1== aero::bit::read(command, CMD_PITCH_UP_GLIDER1) && THIS_DEVICE == ID::G1) || 
                 (1 == aero::bit::read(command, CMD_PITCH_UP_GLIDER2) && THIS_DEVICE == ID::G2) ) {
        to_safety_mode();
      }

    } break;

    // In SAFETY mode, sensors are being polled. Elevons are up and will not move. 
    case MODE_SAFETY: {
      // Do nothing
    } break;

    // Unrecognized mode, state machine should never reach here
    default: {
      bit::set(status.state, STATE_UNDEFINED_MODE);
      message_handler.add_status(status);
    } break;
  }
}

/**
 * @brief Parse a message for commands and take the appropriate action
 */
void parse_cmds(void) {
  int msg_id = static_cast<int>(msg->m_from);
  DEBUG_PRINT("Received radio message from: "); DEBUG_PRINTLN(NAMES[msg_id]);

  // If we received command information
  if(msg->cmds() != NULL) {

    /*
     * PITCH:0 - Glider 1 Pitch Up. Only if THIS_DEVICE == aero::def::G1
     * PITCH:1 - Glider 2 Pitch Up. Only if THIS_DEVICE == aero::def::G2
     * PITCH:6 - Test Comms; Send back empty message aka do nothing on parse. Could add data
     * PITCH:7 - Auto/Manual Mode Swap. 
     */
    
    using namespace aero;
    using namespace aero::def;

    // Extract bit fields
    uint8_t pitch_field = msg->cmds()->pitch;

    // If the command is to initiate a comms test, ignore state. Else pass along command to state machine
    if(pitch_field == CMD_COMMS_TEST) {
        DEBUG_PRINTLN("Comms Test Received");

        if(gps_data.fix == true) {
          bit::set(status.state, STATE_GPS_FIX);
        } else {
          bit::clear(status.state, STATE_GPS_FIX);
        }

        message_handler.add_status(status);
    } else {
      DEBUG_PRINT(pitch_field); DEBUG_PRINTLN(" is the command");
      glider_state_machine(pitch_field);
    }
  } else {
    // No glider commands
  }
}

/**
 * @brief Update the kalman filter values
 * @details Results in a flag being set that lets the auto thread know that new data has been received
 */

void update_controller(void) {
    if(updated == true) {
    
      filter.update(imu_data.gx,imu_data.gy, imu_data.gz, 
                    imu_data.ax, imu_data.ay, imu_data.az,
                    imu_data.mx, imu_data.my, imu_data.mz);

//      if(first_time == true) {
//        first_time = false;
//        offset_pitch = filter.getPitch_rad()*RAD_TO_DEG;
//        offset_roll = filter.getRoll_rad()*RAD_TO_DEG;  
//      }

      new_pitch = filter.getPitch_rad()*RAD_TO_DEG ;
      new_roll =  filter.getRoll_rad()*RAD_TO_DEG ;
      new_yaw =   filter.getYaw_rad()*RAD_TO_DEG;
      
      
      // Set PID inputs
      CONTROLLER::pitch_input = new_pitch;
      CONTROLLER::roll_input  = new_roll;
      CONTROLLER::yaw_input   = new_yaw;
  
      // TODO: Add moving average to the roll, pitch, and yaw values
      DEBUG_PRINT("PID Input: ");
      DEBUG_PRINT("\tRoll: "); DEBUG_PRINT(CONTROLLER::roll_input);
      DEBUG_PRINT("\tPitch: "); DEBUG_PRINT(CONTROLLER::pitch_input);
      DEBUG_PRINT("\tYaw: "); DEBUG_PRINTLN(CONTROLLER::yaw_input);
  
      // Update controller values
      CONTROLLER::update(roll_control, pitch_control, yaw_control);
  
      //CONTROLLER::roll_output = roll_filter.filter(CONTROLLER::roll_output);
      //CONTROLLER::pitch_output = pitch_filter.filter(CONTROLLER::pitch_output);
      //CONTROLLER::yaw_output = yaw_filter.filter(CONTROLLER::yaw_output);
      
      DEBUG_PRINT("PID Output: ");
      DEBUG_PRINT("\tRoll: "); DEBUG_PRINT(CONTROLLER::roll_output);
      DEBUG_PRINT("\tPitch: "); DEBUG_PRINT(CONTROLLER::pitch_output);
      DEBUG_PRINT("\tYaw: "); DEBUG_PRINTLN(CONTROLLER::yaw_output);

      updated  = false;
      
    }
}

void setup() {
  // Initialize serial monitor if required
  DEBUG_START(115200);
  DEBUG_PRINTLN("Setup Starting");

  // Initialization LEDs
  LEDS::init();
  LEDS::on(POWER_LED);
  
  // Initialize sensors
  IMU::init(mpu9250);
  GPS::init(adafruit_gps);
  BARO::init(mpl3115);

  // Initialize servos and receiver input
  ACTUATORS::init(left_elevon, right_elevon, rudder);
  RECEIVER::init();
  RECEIVER::start_interrupts();
  
  // Initialize radio and msg that contains last received radio message
  RADIO::init(radio, RADIO_RESET);
  msg = new aero::def::ParsedMessage_t();

  // Call calibration routines if necessary
  // NOTE: Accel and Mag save results in EEPROM
  if(CALIBRATE_ACCEL) IMU::calibrate(mpu9250, IMU::ACCEL);
  if(CALIBRATE_GYRO)  IMU::calibrate(mpu9250, IMU::GYRO);
  if(CALIBRATE_MAG)   IMU::calibrate(mpu9250, IMU::MAG);
  if(CALIBRATE_BARO)  BARO::calibrate(mpl3115);

  // filter.setInitializationDuration(240000000);
  
  // Initialize PID controllers
  CONTROLLER::init(roll_control, pitch_control, yaw_control);

  // Initialize Setpoint calculator
  SETPOINT::init(TARGET_LAT, TARGET_LON, TARGET_ALT);

  // Initialize threads and add threads
  THREADS::init();

  // Always keep radio, gps, and i2c thread alive
  THREADS::ids[RADIO_ID]  = threads.addThread(thread_radio);
  THREADS::ids[GPS_ID]    = threads.addThread(thread_gps);
  THREADS::ids[I2C_ID]    = threads.addThread(thread_i2c);
  
  // Automatic mode; turn on setpoint and automatic mode threads
  THREADS::ids[SETPOINT_ID] = threads.addThread(thread_setpoint);
  THREADS::ids[AUTO_ID]     = threads.addThread(thread_auto);

  // Manual mode; turn on manual thread
  THREADS::ids[MANUAL_ID] = threads.addThread(thread_manual);

  // Handle boot mode
  // NOTE: threads need to be added for suspend/restart to work
  if(mode == MODE_MANUAL) {
    // If we boot in manual mode, immediately suspend the automatic and setpoint threads
    to_manual_mode();
  } else if(mode == MODE_AUTO) {
    // If we boot in auto mode, immediately suspend the manual thread and terminate interrupts
    to_auto_mode();
  } else {
    to_idle_mode();
  }
    
  // Thread to monitor CPU activity
  THREADS::ids[ACTIVITY_ID] = threads.addThread(thread_activity);

  // // Thread to monitor all data; verbose mode
  // #if defined(VERBOSE_DEBUG)
  //   THREADS::ids[DEBUG_ID] = threads.addThread(thread_debug);
  // #endif 

  // elevons_level();
  DEBUG_PRINTLN("Setup Complete");
}



 
void loop() {
//  radio_curr = millis();
//    if(radio_curr - radio_prev >= RADIO_INTERVAL_MS) { 
//      radio_prev = radio_curr;
//
//      // Keep checking for a new radio message
//      DEBUG_PRINTLN("New Radio Message");
//      RADIO::receive(radio, msg);
//      msg = NULL;
//      DEBUG_PRINTLN("New Radio Message");
//      if( msg != NULL ) {
//        //DEBUG_PRINTLN("New Radio Message");
//        // Only accept message if it was addressed to this grlider
//        if(msg->m_to == THIS_DEVICE) {
//
//          // Build response and set flag if response was succesfully sent
//          server_response = message_handler.build(THIS_DEVICE, aero::def::ID::Gnd);
//
//          LEDS::on(RADIO_LED);
//
//          bool sent = RADIO::respond(radio, server_response);
//
//          LEDS::off(RADIO_LED);
//
//          new_msg = sent;
//        } 
//      }
//    }
    
  // Check for new radio commands
  if(new_msg == true) {
      parse_cmds();
      new_msg = false;
  }

  // For some reason, cannot put filter in thread
  if(new_imu == true) {
    update_controller();
    new_imu = false;
  }
}

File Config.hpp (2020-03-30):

#pragma once

/**
 * File for containing all configuration variables such as pins, constants
 */
 
#include "Arduino.h"
#include "src/aero-cpp-lib/include/Data.hpp"


using Pin = unsigned int;

static constexpr float TARGET_LAT = 0.0f;
static constexpr float TARGET_LON = 0.0f;
static constexpr float TARGET_ALT = 0.0f;

enum mode_type {MODE_IDLE = 0, MODE_MANUAL = 1, MODE_AUTO = 2, MODE_SAFETY = 3};
static constexpr mode_type DEFAULT_MODE = MODE_AUTO;

// Commands
static constexpr uint8_t CMD_PITCH_UP_GLIDER1 = 0x00; // Glider 1 Emergency Pitch Up; Only if this device is G1.
static constexpr uint8_t CMD_PITCH_UP_GLIDER2 = 0x01; // Glider 2 Emergency Pitch Up; Only if this device is G2.
static constexpr uint8_t CMD_TOGGLE_ENGAGE    = 0x05;
static constexpr uint8_t CMD_COMMS_TEST       = 0x06; // Glider Communications Check. Can also be used to send back data.
static constexpr uint8_t CMD_MODE_SWAP        = 0x07; // Glider Mode Swap. Auto/Manual mode toggle.

static constexpr uint8_t STATE_GPS_FIX = 0x00; // Bit 0 for GPS fix
static constexpr uint8_t STATE_ENGAGED_MODE = 0x1E; // Bit 30 for engage mode
static constexpr uint8_t STATE_UNDEFINED_MODE = 0x1F; // Bit 31 for undefined mode

static constexpr float ALLOWABLE_AZIMUTH_ERROR = 3.0f;
static constexpr float ALLOWABLE_ELEVATION_ERROR = 3.0f;

#define  DEBUG
//#define  VERBOSE_DEBUG
//#define  TEST_TRAINER
#define FINAL_GLIDER

#ifdef DEBUG
    #define DEBUG_PRINT(x) Serial.print(x)
    #define DEBUG_PRINTLN(x) Serial.println(x)
    #define DEBUG_START(x) Serial.begin(x); delay(1000)
#else
    #define DEBUG_PRINT(x)
    #define DEBUG_PRINTLN(x)
    #define DEBUG_START(x)
#endif

#if defined(FINAL_GLIDER)
    static constexpr unsigned long LEFT_ELEVON_MS_OFFSET = 0;
    static constexpr unsigned long RIGHT_ELEVON_MS_OFFSET = 0;

    static constexpr float SERVO_MIN_MS = 800.0f;
    static constexpr float SERVO_MAX_MS = 2000.0f;

#elif defined(TEST_GLIDER)
    static constexpr unsigned long LEFT_ELEVON_MS_OFFSET = 0;
    static constexpr unsigned long RIGHT_ELEVON_MS_OFFSET = 0;

    static constexpr float SERVO_MIN_MS = 800.0f;
    static constexpr float SERVO_MAX_MS = 2000.0f;

#elif defined(TEST_TRAINER)
    static constexpr unsigned long LEFT_ELEVON_MS_OFFSET = 40;   // Pitch
    static constexpr unsigned long RIGHT_ELEVON_MS_OFFSET = 50; // Roll

    static constexpr float SERVO_MIN_MS = 900.0f;
    static constexpr float SERVO_MAX_MS = 2100.0f;
#else 
    static constexpr unsigned long LEFT_ELEVON_MS_OFFSET = 0;
    static constexpr unsigned long RIGHT_ELEVON_MS_OFFSET = 0;

    static constexpr float SERVO_MIN_MS = 800.0f;
    static constexpr float SERVO_MAX_MS = 2000.0f;
#endif

/* DEVICE NAMES */
const String NAMES[] = {"GND", "PLANE", "G1", "G2"};

/* CALIBRATION FLAGS */
static constexpr bool CALIBRATE_ACCEL = false;
static constexpr bool CALIBRATE_GYRO = true;
static constexpr bool CALIBRATE_MAG = false;
static constexpr bool CALIBRATE_BARO = true;

/* BOOT MODE */ 
enum class BOOT_MODE {LED_TEST, LED_TEST_RANDOM};
static constexpr BOOT_MODE MODE = BOOT_MODE::LED_TEST_RANDOM;

/* PID */
static constexpr double ROLL_KP = 3.0f, ROLL_KI = 0.00f, ROLL_KD = 0.0f;
static constexpr double PITCH_KP = 8.0f, PITCH_KI = 0.00f, PITCH_KD = 0.0f;
static constexpr double YAW_KP = 1.0f, YAW_KI = 0.00f, YAW_KD = 0.0f;

static constexpr double DEFAULT_ROLL_SETPOINT = 0;
static constexpr double ROLL_MIN_LIMIT = -90;
static constexpr double ROLL_MAX_LIMIT = 90;

static constexpr double DEFAULT_PITCH_SETPOINT = 8;
static constexpr double PITCH_MIN_LIMIT = -90;
static constexpr double PITCH_MAX_LIMIT = 90;

static constexpr double DEFAULT_YAW_SETPOINT = 0;
static constexpr double YAW_MIN_LIMIT = -90;
static constexpr double YAW_MAX_LIMIT = 90;

static constexpr bool INVERT_PID = true;

/* BAROMETER */
static constexpr double ALTITUDE_BIAS = 238.0f; // In metres

// Sampling intervals of 0=6 ms , 1=10, 2=18, 3=34, 4=66, 5=130, 6=258, and 7=512
static constexpr unsigned long OVER_SAMPLE_PERIODS_MS[] = {6, 10, 18, 34, 66, 130, 258, 512};
static constexpr int OVER_SAMPLE_RATIO = 7;

/* SYSTEM FLAGS */
static constexpr bool DEBUG_MODE = true;  // Block usage of Serial printing if not debugging to speed up system

/* LEDS */
static constexpr Pin LED1 = 8;
static constexpr Pin LED2 = 7;
static constexpr Pin LED3 = 6;
static constexpr Pin LED4 = 5;
static constexpr unsigned int LED_COUNT = 4;
static constexpr Pin LED_PINS[LED_COUNT] = {LED1, LED2, LED3, LED4};

/* FROM LEFT TO RIGHT */
static constexpr Pin POWER_LED = LED1;    // On when board is powered
static constexpr Pin ACTIVITY_LED = LED2; // Toggles on and off to signal that the CPU is running
static constexpr Pin RADIO_LED = LED3;    // Turns on when new message is received
static constexpr Pin MODE_LED = LED4;     // On when in manual mode, else off
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

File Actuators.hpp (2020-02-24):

#pragma once

/**
 * File to encapsulate functions that interface with the servos
 * Makes use of the Arduino Servo library 
 */
#include <Servo.h>

/**
 * Actuator namespace; encapsulates all related functions
 */
namespace ACTUATORS {

  /**
   * @brief Initializes each servo object by attaching it to the appropriate pin
   * 
   * @param left_elevon servo object reference representing the left elevon
   * @param right_elevon servo object reference representing the right elevon
   * @param rudder servo object reference representing the rudder
   */
  inline void init(Servo& left_elevon, Servo& right_elevon, Servo& rudder) {
    left_elevon.attach(SERVO1);
    right_elevon.attach(SERVO2);
    rudder.attach(SERVO3);
  }

  /**
   * @brief Function to test servo functionality by sweeping servos up and down
   * 
   * @param left left elevon servo
   * @param right right elevon servo
   */
  inline void sweep(Servo& left, Servo& right) {
    static int angle = 0;
    static int delta = 1;
    static bool left_flag = true;

    if(angle >= 180) {
      delta = -1;
    } else if(angle <= 0) {
      delta = 1;
    }

    if(left_flag) {
      left_flag = !left_flag;
      left.write(angle);
    } else {
      left_flag = !left_flag;
      right.write(angle);
    }
    
    angle += delta;
  }

  /**
   * @brief Command a servo to move using pulse width
   * 
   * @param motor object pertaining to which servo you want to move
   * @param ms width of pulse to send to servo
   */
  inline void command_ms(Servo& motor, unsigned long ms) {
    motor.writeMicroseconds(ms);
  }

  /**
   * @brief Command a servo to move using angle
   * 
   * @param motor object pertaining to which servo you want to move
   * @param deg angle to send to servo
   */
  inline void command_deg(Servo& motor, float deg) {
    motor.write(deg);
  }
}

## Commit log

2019-11-16 First revision of schematic
    [capstone.brd, capstone.sch]
2019-11-17 Finished board routing
    [capstone.brd, capstone.sch]
2019-12-02 Finalize board
    [capstone.brd, capstone.sch]
2020-01-08 new board
    [capstone.brd, capstone.sch, schematic.sch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]
2020-01-10 added manufacturing files
    [copper_bottom.gbr, copper_top.gbr, drill_1_16.xln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]
2020-01-17 Basic led test and working on receiver interrupt code
2020-01-22 Added sensor support, servo support, led support, and filtering
2020-01-24 added pid
2020-01-26 thread setup; radio comms
2020-01-28 version 3 of the board; hooked up interrupt pin and added an extra servo
    [schematic.sch, untitled.brd, untitled.dxf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]
2020-01-31 mode swap tested, seems to be working
    [capstone.ino]
2020-01-31 pitch command
2020-02-05 basic servo working; also added gerber files
    [copper_bottom.gbr, copper_top.gbr, drill_1_16.xln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]
2020-02-10 added baro calibration
2020-02-11 playing around with constants and values for fixed wing model
    [Config.hpp, capstone.ino]
2020-02-12 added screw terminal to board; combined filter with imu scope
    [untitled.brd, untitled.sch]
2020-02-12 imu refractoring; code not compiling
2020-02-12 code compiling for imu now; need to test
2020-02-13 verified v4 - final design pins and started clean up for report
    [capstone.brd, capstone.sch, schematic.sch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]
2020-02-15 board update
    [copper_bottom.gbr, copper_top.gbr, drill_1_16.xln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]
2020-02-16 getting imu to work again
2020-02-16 Schematic Cleanup
    [capstone.brd, capstone.sch, schematic.sch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]
2020-02-16 add test points to final design
    [capstone.brd, capstone.sch]
2020-02-16 finalized board design for final design
    [capstone.brd, capstone.sch]
2020-02-17 updated glider design circuit board
2020-02-24 design update for hardware
    [capstone-100components.xlsx, capstone-10components.xlsx, capstone-25components.xlsx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]
2020-03-02 setpoint and pitch up written

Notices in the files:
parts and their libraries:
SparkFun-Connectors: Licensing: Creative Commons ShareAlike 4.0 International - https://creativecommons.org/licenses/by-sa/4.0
